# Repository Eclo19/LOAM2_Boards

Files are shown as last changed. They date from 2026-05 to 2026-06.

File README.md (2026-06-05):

# LOAM2_Boards_Winter/Spring_2026

## Description
These files contain the progress done on drone hardware for the LOAM 2 project. The current strategy is to produce a support board that connects to the Pixhawk's FMU, communicates with the nodes, and hosts many other vital systems. This board should concentrate as many of the drone peripherals as possible in a single PCB to ensure robustness. The support board contains the following sub-systems:

 * Power management and battery monitoring (PM)
 * GPS
 * ARM Switch
 * nRF54L15 (MCU)
 * nRF21540 (FEM)
 * GPS patch antenna
 * Bluetooth antenna (not certain yet)
 * JST Connectors for the FMU harness
 * Debug taps for all outputs

## Power Management

The power management issue is mostly solved. The board stored in `power_management_tests` was produced and thoroughly tested. We confirmed its outputs were the expected 3.3 and 5V, it handled the throuttle of the drone motors, and voltage and current readings are in agreement with lab equipment. **Note:** To ensure proper voltage and current readings, the resistor ratios implemented in the voltage and current sensors must be taken into account by the software. In Ardupilot, simply set `BATT_VOLT_MULT = 5.667` and `BATT_AMP_PERVLT = 25.0`. The chosen buck-converters can output currents of up to 3 A, far more than the FMU or the support board systems might draw. 

When redoing the layout for this board in the support board, make sure to follow IC datasheet recommendations and lay thick traces in the battery input and output ports, which can draw large currents (~80 A). 

## GPS

The GPS schematics were adapted from this repository: https://github.com/ZIOCC/Zio-Qwiic-GPS-Module-U-blox-NEO-M8N-0-10). They leverage the NEO-M8N-0 chip and a patch antenna at the GPS band of 1575.42 MHz. 

## Arm Switch

This replaces the floating ARM switch in the Pixhawk. 

## MCU and FEM

The drone communicates with node sensors through the nRF54L15 MCU using BLE. Currently, we assume the nodes will also host this MCU, as inter-communication between this IC is simple. The MCU is powered by the 3.3 V power line produced by the PM. Communication with the FMU is done through the TELEM2 port, which connects through UART to pins on the suppoart board MCU. 

The current drone wake-up strategy is to rely on energy harvesting to charge the base of an $npn$ transistor (2N3904) above its $V_{th}$, flipping the collector voltage from 3.3 V to 0 when charged, thus waking up the node. The node MCU must handle this and a few nuances regarding oscillation (described in our report) in firmware. We used the AEM30940 DK for our energy harvesting tests on the chosen band of 2.45 GHz. To ensure enough energy can be transmitted to charge the base of the transistor to around 0.65 V, a decent amount of power must be received. The The 47 C.F.R. § 15.247 permits a maximum of 1 W (30 dBm) of transmission power for the 2.45 GHz band given a few constraints, and the nRF54L15 can ony output a maximum of 8 dBm. To increase transmission power, we connect an RF FEM, the nRF21540, a bidirectional FEM (LNA for Rx and PA for Tx, with shiwtching controlled by GPIO pins or SPI). The antenna choice is still a major question for this transmission. 

The drone MCU in the suppoart board is programmed through an SWD interface. 

## Connectors and Debug Taps

The support board hosts multiple connectors that should be tightly packed in a harness connected to the FMU. These include the following ports: GPS, TELEM2, SWITCH, and POWER. Our initial connector selection was a DF13, but these are not fully compatible. We believe the correct connectors are JST. For testing and debugging reasons, it is helpful to pack debup taps for many essential nodes in the system (e.g. 3V3, 5V, CURRENT_SENSE, RX_GPS, etc). 

## Layout Notes

The layout of the support board has just started at the time of this README.md file. Like in the power management test board, the support board has DRCs from JLC PCB, imported from https://github.com/sethhillbrand/kicad_templates/tree/master. This board has 4 layers though, as opposed to the simple 2-layer power management tests board.

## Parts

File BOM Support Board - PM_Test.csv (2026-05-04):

Reference | Qty | Value | Manufacturer | Manufacturer Product Number | Description | Footprint | Datasheet | Notes
C501,C502 | 2 | 10 u | Murata Electronics | CAP CER 10UF 6.3V X5R 0603 | CAP CER 10UF 6.3V X5R 0603 | Capacitor_SMD:C_0603_1608Metric_Pad1.08x0.95mm_HandSolder | ~
C503,C505,C510,C512,C516,C517, | 6 | 100n | Samsung Electro-Mechanics | CL10E104KC8VPNC | CAP CER 100NF 100V X8L 0603 | Capacitor_SMD:C_0603_1608Metric_Pad1.08x0.95mm_HandSolder | ~
C504,C511 | 2 | 22 n | Samsung Electro-Mechanics | CL10B223KB8WPNC | CAP CER 0.022UF 50V X7R 0603 | Capacitor_SMD:C_0603_1608Metric_Pad1.08x0.95mm_HandSolder | ~
C506,C507,C509,C513,C514 | 5 | 22µ | Venkel | C0805X5R350-226MNE-CT | Chip Capacitor,0805,X5R,35V,22uF | Capacitor_SMD:C_0805_2012Metric_Pad1.18x1.45mm_HandSolder | ~
C508 | 1 | 470p | Samsung Electro-Mechanics | CL10C471JB8NNNC | CAP CER 470PF 50V C0G/NP0 0603 | Capacitor_SMD:C_0603_1608Metric_Pad1.08x0.95mm_HandSolder | ~
C515 | 1 | 300p | KYOCERA AVX | 06035A301JAT2A | CAP CER 300PF 50V NP0 0603 | Capacitor_SMD:C_0603_1608Metric_Pad1.08x0.95mm_HandSolder | ~
C518 | 1 | 1µ | Samsung Electro-Mechanics | CL10B105KP8NNNC | CAP CER 1UF 10V X7R 0603 | Capacitor_SMD:C_0603_1608Metric_Pad1.08x0.95mm_HandSolder | ~
D1 | 1 | RED | Rohm Semiconductor | SML-D12U1WT86 | LED RED DIFFUSED 1608 SMD | LED_SMD:LED_0603_1608Metric_Pad1.05x0.95mm_HandSolder | ~
D2 | 1 | Yellow | Rohm Semiconductor | SML-D12Y1WT86 | LED YELLOW DIFFUSED 1608 SMD | LED_SMD:LED_0603_1608Metric_Pad1.05x0.95mm_HandSolder | ~
J1,J4 | 2 | Conn_01x02_Socket |  |  |  | Connector_Wire:SolderWire-6sqmm_1x02_P14mm_D3.5mm_OD7mm | ~
J2,J3,J6,J7 | 4 | Conn_01x02_Socket |  |  |  | Connector_Wire:SolderWire-0.75sqmm_1x02_P7mm_D1.25mm_OD3.5mm | ~
J5 | 1 | Conn_01x06_Pin | Hirose Electric Co Ltd | DF13-6P-1.25DSA(05) | CONNECTOR | Connector_Hirose:Hirose_DF13-06P-1.25DSA_1x06_P1.25mm_Vertical | ~
J505 | 1 | Conn_01x01_Socket |  |  |  | Connector_Wire:SolderWire-0.75sqmm_1x01_D1.25mm_OD3.5mm | ~
L501,L502 | 2 | 6.8µH | TDK | MLZ2012N6R8LT000 | FIXED IND 6.8UH 550MA 250 MOHM | Inductor_SMD:L_0805_2012Metric_Pad1.05x1.20mm_HandSolder | ~
R501,R507 | 2 | 191k | YAGEO | RC0603FR-07191KL | RES 191K OHM 1% 1/10W 0603 | Resistor_SMD:R_0603_1608Metric_Pad0.98x0.95mm_HandSolder | ~
R502,R508 | 2 | 49.9k | YAGEO | RC0603FR-0749K9L | RES 49.9K OHM 1% 1/10W 0603 | Resistor_SMD:R_0603_1608Metric_Pad0.98x0.95mm_HandSolder | ~
R503 | 1 | 100k | YAGEO | RC0603FR-07100KL | RES 100K OHM 1% 1/10W 0603 | Resistor_SMD:R_0603_1608Metric_Pad0.98x0.95mm_HandSolder | ~
R504,R509,R510,R511 | 4 | 10k | YAGEO | RC0603FR-0710KL | RES 10K OHM 1% 1/10W 0603 | Resistor_SMD:R_0603_1608Metric_Pad0.98x0.95mm_HandSolder | ~
R505 | 1 | 9.09k | YAGEO | RC0603FR-079K09L | RES 9.09K OHM 1% 1/10W 0603 | Resistor_SMD:R_0805_2012Metric_Pad1.20x1.40mm_HandSolder | ~
R506 | 1 | 51k | YAGEO | RC0603FR-0751KL | RES 51K OHM 1% 1/10W 0603 | Resistor_SMD:R_0603_1608Metric_Pad0.98x0.95mm_HandSolder | ~
R512 | 1 | 90.9k | YAGEO | RC0603FR-0790K9L | RES 90.9K OHM 1% 1/10W 0603 | Resistor_SMD:R_0603_1608Metric_Pad0.98x0.95mm_HandSolder | ~
R513 | 1 | 56k | YAGEO | RC0603FR-0756KL | RES 56K OHM 1% 1/10W 0603 | Resistor_SMD:R_0603_1608Metric_Pad0.98x0.95mm_HandSolder | ~
R514 | 1 | 12k | YAGEO | RC0603FR-0712KL | RES 12K OHM 1% 1/10W 0603 | Resistor_SMD:R_0603_1608Metric_Pad0.98x0.95mm_HandSolder | ~
R515 | 1 | 0.5m | Vishay Dale | WSLF2512L5000FEB | RES SMD 500 UOHM 1% 6W 2512 | Resistor_SMD:R_2512_6332Metric_Pad1.40x3.35mm_HandSolder | ~
R516 | 1 | 80k | Vishay Dale Thin Film | PTN0603E8002BST1 | RES 80K OHM 0.1% 0.15W 0603 | Resistor_SMD:R_0603_1608Metric_Pad0.98x0.95mm_HandSolder
R517,R518 | 2 | 1K ±1% | YAGEO | RC0603FR-071KL | RES 1K OHM 1% 1/10W 0603 | Resistor_SMD:R_0603_1608Metric_Pad0.98x0.95mm_HandSolder
U501,U502 | 2 | ~ | Monolithic Power Systems Inc. | MP2338GTL-Z | IC REG BUCK ADJ 3A SOT583 | Package_TO_SOT_SMD:SOT-583-8
U503 | 1 | INA169 | Texas Instruments | INA169NA/3K | IC CURRENT MONITOR 0.5% SOT23-5 | Package_TO_SOT_SMD:SOT-23-5 | http://www.ti.com/lit/ds/symlink/ina169.pdf
U504 | 1 | MCP6002T-E/OT | Microchip Technology | MCP6002-I/P | IC OPAMP GP 2 CIRCUIT 8DIP | Package_DIP:DIP-8_W7.62mm_LongPads | https://ww1.microchip.com/downloads/en/DeviceDoc/MCP6001-1R-1U-2-4-1-MHz-Low-Power-Op-Amp-DS20001733L.pdf

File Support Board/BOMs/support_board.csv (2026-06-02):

Reference | Qty | Value | DNP | Exclude from BOM | Exclude from Board | Footprint | Datasheet
C101 | 1 | 22pF ±10% 50V |  |  |  | Capacitor_SMD:C_0402_1005Metric_Pad0.74x0.62mm_HandSolder
C102 | 1 | 33pF ±10% 50V |  |  |  | Capacitor_SMD:C_0402_1005Metric_Pad0.74x0.62mm_HandSolder
C103 | 1 | 4.7uF ±10% 10V |  |  |  | Capacitor_SMD:C_0402_1005Metric_Pad0.74x0.62mm_HandSolder
C104,C105,C107,C110 | 4 | 100nF ±10% 50V |  |  |  | Capacitor_SMD:C_0402_1005Metric_Pad0.74x0.62mm_HandSolder
C106 | 1 | 10uF ±10% 10V |  |  |  | Capacitor_SMD:C_0402_1005Metric_Pad0.74x0.62mm_HandSolder
C108 | 1 | XH414HG-IV01E |  |  |  | Capacitor_SMD:C_1210_3225Metric
C301,C302 | 2 | 12pF |  |  |  | Capacitor_SMD:C_0402_1005Metric_Pad0.74x0.62mm_HandSolder | ~
C303,C305,C306,C307,C308 | 5 | 100nF |  |  |  | Capacitor_SMD:C_0402_1005Metric_Pad0.74x0.62mm_HandSolder | ~
C304 | 1 | 22 uF |  |  |  | Capacitor_SMD:C_0603_1608Metric_Pad1.08x0.95mm_HandSolder | ~
C309 | 1 | 0.3pF |  |  |  | Capacitor_SMD:C_0603_1608Metric_Pad1.08x0.95mm_HandSolder | ~
C310 | 1 | 0.5pF |  |  |  | Capacitor_SMD:C_0402_1005Metric_Pad0.74x0.62mm_HandSolder | ~
C311 | 1 | 10nF |  |  |  | Capacitor_SMD:C_0402_1005Metric_Pad0.74x0.62mm_HandSolder | ~
C501,C502 | 2 | 10 u |  |  |  | Capacitor_SMD:C_01005_0402Metric_Pad0.57x0.30mm_HandSolder | ~
C503,C510,C516,C517 | 4 | 100n |  |  |  | Capacitor_SMD:C_01005_0402Metric_Pad0.57x0.30mm_HandSolder | ~
C504,C511 | 2 | 22 n |  |  |  | Capacitor_SMD:C_01005_0402Metric_Pad0.57x0.30mm_HandSolder | ~
C505,C512 | 2 | 100 n |  |  |  | Capacitor_SMD:C_01005_0402Metric_Pad0.57x0.30mm_HandSolder | ~
C506,C513 | 2 | 22u |  |  |  | Capacitor_SMD:C_01005_0402Metric_Pad0.57x0.30mm_HandSolder | ~
C507,C514 | 2 | 22µ |  |  |  | Capacitor_SMD:C_01005_0402Metric_Pad0.57x0.30mm_HandSolder | ~
C508 | 1 | 470p |  |  |  | Capacitor_SMD:C_01005_0402Metric_Pad0.57x0.30mm_HandSolder | ~
C509 | 1 | 22 u |  |  |  | Capacitor_SMD:C_01005_0402Metric_Pad0.57x0.30mm_HandSolder | ~
C515 | 1 | 300p |  |  |  | Capacitor_SMD:C_01005_0402Metric_Pad0.57x0.30mm_HandSolder | ~
C518 | 1 | 1µ |  |  |  | Capacitor_SMD:C_01005_0402Metric_Pad0.57x0.30mm_HandSolder | ~
D101 | 1 | RB520S30T1G |  |  |  | Diode_SMD:D_SOD-523
D103 | 1 | GREEN |  |  |  | LED_SMD:LED_0603_1608Metric
D201,D501 | 2 | RED |  |  |  | LED_SMD:LED_0603_1608Metric | ~
D502 | 1 | YELLOW |  |  |  | LED_SMD:LED_0603_1608Metric
E101 | 1 | APAE1575R1820ABDC1-T |  |  |  | support_board:XDCR_APAE1575R1820ABDC1-T
GPS_CONN1,POWER_CONN1,TELEM2_CONN1 | 3 | Conn_01x06_Socket |  |  |  | Connector_Hirose:Hirose_DF13-06P-1.25DSA_1x06_P1.25mm_Vertical | ~
GPS_DEBUG1 | 1 | Conn_01x04_Socket |  |  |  | Connector_Wire:SolderWire-0.75sqmm_1x04_P4.8mm_D1.25mm_OD2.3mm | ~
J301 | 1 | Conn_Coaxial |  |  |  | Connector_Coaxial:U.FL_Hirose_U.FL-R-SMT-1_Vertical | ~
J302 | 1 | Conn_ARM_SWD_TagConnect_TC2030-NL |  | Excluded from BOM |  | Connector:Tag-Connect_TC2030-IDC-NL_2x03_P1.27mm_Vertical | https://www.tag-connect.com/wp-content/uploads/bsk-pdf-manager/TC2030-CTX_1.pdf
J503,J504,J505 | 3 | Conn_01x01_Socket |  |  |  | Connector_Wire:SolderWire-0.75sqmm_1x01_D1.25mm_OD3.5mm | ~
L101 | 1 | 22uH ±10% |  |  |  | Inductor_SMD:L_0603_1608Metric
L301 | 1 | 2nH |  |  |  | Inductor_SMD:L_0402_1005Metric_Pad0.77x0.64mm_HandSolder | ~
L501,L502 | 2 | 6.8µH |  |  |  | Inductor_SMD:L_0402_1005Metric | ~
R101,R107,R109 | 3 | 1K ±1% |  |  |  | Resistor_SMD:R_0402_1005Metric_Pad0.72x0.64mm_HandSolder
R102,R103 | 2 | 10K ±1% |  |  |  | Resistor_SMD:R_0402_1005Metric_Pad0.72x0.64mm_HandSolder
R104,R105 | 2 | 4.7K ±1% |  |  |  | Resistor_SMD:R_0402_1005Metric_Pad0.72x0.64mm_HandSolder
R108 | 1 | 22R ±1% |  |  |  | Resistor_SMD:R_0402_1005Metric_Pad0.72x0.64mm_HandSolder
R201 | 1 | 220 |  |  |  | Resistor_SMD:R_0402_1005Metric_Pad0.72x0.64mm_HandSolder | ~
R301 | 1 | 10k |  |  |  | Resistor_SMD:R_0402_1005Metric_Pad0.72x0.64mm_HandSolder | ~
R302,R303 | 2 | 100 |  |  |  | Resistor_SMD:R_0402_1005Metric_Pad0.72x0.64mm_HandSolder | ~
R501,R507 | 2 | 191k |  |  |  | Resistor_SMD:R_0603_1608Metric_Pad0.98x0.95mm_HandSolder | ~
R502,R508 | 2 | 49.9k |  |  |  | Resistor_SMD:R_0603_1608Metric_Pad0.98x0.95mm_HandSolder | ~
R503 | 1 | 100k |  |  |  | Resistor_SMD:R_0603_1608Metric_Pad0.98x0.95mm_HandSolder | ~
R504,R509,R510,R511,R516 | 5 | 10k |  |  |  | Resistor_SMD:R_0603_1608Metric_Pad0.98x0.95mm_HandSolder | ~
R505 | 1 | 9.09k |  |  |  | Resistor_SMD:R_0603_1608Metric_Pad0.98x0.95mm_HandSolder | ~
R506 | 1 | 51k |  |  |  | Resistor_SMD:R_0603_1608Metric_Pad0.98x0.95mm_HandSolder | ~
R512 | 1 | 90.9k |  |  |  | Resistor_SMD:R_0603_1608Metric_Pad0.98x0.95mm_HandSolder | ~
R513 | 1 | 56k |  |  |  | Resistor_SMD:R_0603_1608Metric_Pad0.98x0.95mm_HandSolder | ~
R514 | 1 | 12k |  |  |  | Capacitor_SMD:C_0805_2012Metric_Pad1.18x1.45mm_HandSolder | ~
R515 | 1 | 4m |  |  |  | Resistor_SMD:R_0603_1608Metric_Pad0.98x0.95mm_HandSolder | ~
R517,R518 | 2 | 1K ±1% |  |  |  | Resistor_SMD:R_0603_1608Metric_Pad0.98x0.95mm_HandSolder
SWITCH1 | 1 | 1825910-6 |  |  |  | support_board:SW_1825910-6-4
SWITCH_CONN1 | 1 | Conn_01x03_Socket |  |  |  | Connector_Hirose:Hirose_DF13-03P-1.25DSA_1x03_P1.25mm_Vertical | ~
SWITCH_DEBUG1 | 1 | Conn_01x03_Socket |  |  |  | Connector_Wire:SolderWire-0.75sqmm_1x03_P4.8mm_D1.25mm_OD2.3mm | ~
TELEM_2_DEBUG1 | 1 | Conn_01x02_Socket |  |  |  | Connector_Wire:SolderWire-0.75sqmm_1x02_P4.8mm_D1.25mm_OD2.3mm | ~
U101 | 1 | NEO-M8N |  |  |  | support_board:NEO-M8N-0
U102 | 1 | SC16IS752 |  |  |  | support_board:SC16IS752
U301 | 1 | nRF54L15-QFXX |  |  |  | Package_DFN_QFN:QFN-48-1EP_6x6mm_P0.4mm_EP4.6x4.6mm | https://docs.nordicsemi.com/bundle/ps_nrf54L15
U501,U502 | 2 | MP2338 |  |  |  | Package_TO_SOT_SMD:SOT-583-8
U503 | 1 | INA169 |  |  |  | Package_TO_SOT_SMD:SOT-23-5 | http://www.ti.com/lit/ds/symlink/ina169.pdf
U504 | 1 | MCP6002T-E/OT |  |  |  | Package_DIP:DIP-8_W7.62mm_LongPads | https://ww1.microchip.com/downloads/en/DeviceDoc/MCP6001-1R-1U-2-4-1-MHz-Low-Power-Op-Amp-DS20001733L.pdf
X101 | 1 | 3.072MHZ |  |  |  | Crystal:Crystal_SMD_HC49-SD
X201 | 1 | Crystal_GND24 |  |  |  | Crystal:Crystal_SMD_2016-4Pin_2.0x1.6mm | ~

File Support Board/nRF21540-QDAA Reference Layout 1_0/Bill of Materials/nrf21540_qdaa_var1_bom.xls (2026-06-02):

Bill of material
Board: | nRF21540 Reference Layout Alt. 1
Version: | 1.0
Designator | Value | Description | Footprint Doc
C1, C3 | 1.0pF | Capacitor, NP0, ±0.05pF, 50V | 0201
C2 | 2.0pF | Capacitor, NP0, ±0.05pF, 25V | 0201
C6 | 100nF | Capacitor, X5R, ±10% | 0201
C7 | 10µF | Capacitor, X5R, ±20% | 0603
L1 | 1.9nH | Inductor, 600mA, ±0.1ｎH, 120mOhm | 0201
L2 | 3.0nH | Inductor, 600mA, ±0.1ｎH, 120mOhm | 0201
R1 | 33k | Resistor, ±1%, 0.05W | 0201
R2 | 49.9R | Resistor, ±1%, 0.05W | 0201
U1 | nRF21540-QDAA | Radio front-end / range extender for 2.4GHz | QFN-16

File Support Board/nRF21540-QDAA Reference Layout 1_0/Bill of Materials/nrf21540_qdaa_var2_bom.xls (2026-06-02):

Bill of material
Board: | nRF21540 Reference Layout Alt. 2
Version: | 1.0
Designator | Value | Description | Footprint Doc
C1, C3, C5 | 1.0pF | Capacitor, NP0, ±0.05pF, 50V | 0201
C2, C4 | 2.0pF | Capacitor, NP0, ±0.05pF, 25V | 0201
C6 | 100nF | Capacitor, X5R, ±10% | 0201
C7 | 10µF | Capacitor, X5R, ±20% | 0603
L1, L3 | 1.9nH | Inductor, 600mA, ±0.1ｎH, 120mOhm | 0201
L2, L4 | 3.0nH | Inductor, 600mA, ±0.1ｎH, 120mOhm | 0201
R1 | 33k | Resistor, ±1%, 0.05W | 0201
U1 | nRF21540-QDAA | Radio front-end / range extender for 2.4GHz | QFN-16

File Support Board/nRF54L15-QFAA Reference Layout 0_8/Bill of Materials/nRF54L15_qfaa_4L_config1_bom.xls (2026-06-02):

Bill of material
Device: | nRF54L15-QFAA
Title: | Reference Layout
Version: | v0.8
Designator | Value | Description | Assembly | Footprint Doc
C1, C2 | 2.2µF | Capacitor, Ceramic, 2.2µF 2.5V X6T 0201,±20% |  | 0201
C3 | 10µF | Capacitor, X6S, ±20%, 6.3V |  | 0402
C4, C7, C8, C10 | 100nF | Capacitor, X7R, ±10% |  | 0201
C5 | 2.2nF | Capacitor, X7R, ±10%, 10V |  | 0201
C6 | 1.5pF | Capacitor, NP0, ±0.05pF, 25V |  | 0201
C9 | 2.0pF | Capacitor, NP0, ±0.05pF, 25V |  | 0201
C11 | 0.3pF | Capacitor, C0G, ±0.1pF, 50V |  | 0201
C12 | 10nF | Capacitor, X7R, 6.3V |  | 0201
C13 | 3.9pF | Capacitor, NP0, ±0.05pF, 25V |  | 0201
FB1 | 120R/0.2A | Ferrite Bead, 120 Ohm @ 100MHz, 200mA, 500 mOhm Max |  | 0201
L1 | 4.7µH | Inductor, 120mA, ±20%, 0.65R |  | 0603
L2 | 2.7nH | Inductor, 600mA, ±0.1ｎH, 120mOhm |  | 0201
L3, L4 | 3.5nH | Inductor, 500mA, ±0.1ｎH, 170mOhm |  | 0201
R1 | 1k | Resistor, ±1%, 0.05W |  | 0201
U1 | nRF54L15-QFAA | Multi-protocol Bluetooth Low Energy, IEEE 802.15.4 and 2.4GHz proprietary Wireless MCU |  | QFN-48
X1 | 32.768kHz | XTAL SMD 2012, 32.768kHz, 9pF, ±20ppm |  | XTAL_2012
X2 | 32MHz | XTAL SMD 2016, 32MHz, Cl=8pF, Tot: ±40ppm |  | XTAL_2016

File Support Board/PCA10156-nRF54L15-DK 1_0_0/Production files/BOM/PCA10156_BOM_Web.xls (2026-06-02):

Bill of material
Board: | PCA10156
Version: | 1.0.0
Designator | Value | Description | Assembly | Footprint Doc | Manufacturer | Manufacturer Part Number
C1, C2 | 2.2µF | Capacitor, Ceramic, 2.2µF 2.5V X6T 0201,±20% |  | 0201 | Murata | GRM033R61A225KE47
C3 | 10µF | Capacitor, X6S, ±20%, 6.3V |  | 0402 | N.A. | N.A.
C4, C7, C8, C10, C11, C13, C14, C15, C18, C20, C21, C22, C25, C29, C34, C35, C36, C37, C44, C46, C48, C49, C52, C53, C55, C56, C57, C62, C63, C64, C65, C66, C69, C70, C72, C73, C74, C75, C76, C77, C78, C79 | 100nF | Capacitor, X5R, ±10% |  | 0201 | N.A. | N.A.
C5, C33 | 2.2nF | Capacitor, X7R, ±10%, 10V |  | 0201 | N.A. | N.A.
C6 | 1.5pF | Capacitor, NP0, ±0.05pF, 25V, High Q |  | 0201 | Murata | GJM0335C1E1R5WB01
C9 | 2.0pF | Capacitor, NP0, ±0.05pF, 25V |  | 0201 | Murata | GJM0335C1E2R0WB01
C12, C30 | 10nF | Capacitor, X7R, ±10% |  | 0201 | N.A. | N.A.
C16, C28, C31, C32, C39, C45, C50, C51, C68 | 1.0µF | Capacitor, X5R, ±10%, 6.3V |  | 0402 | N.A. | N.A.
C17, C19 | 300pF | Capacitor, C0G, ±5%, 50V |  | 0402 | N.A. | N.A.
C23 | 2.2µF | Capacitor, X5R, ±10% |  | 0402 | N.A. | N.A.
C24, C26, C27 | 10µF | Capacitor, X7T, ±20%, 10V |  | 0603 | Murata | GRM188D71A106MA73
C38 | 1.4pF | Capacitor, C0G, ±0.05pF, 25V |  | 0201 | Murata | GJM0335C1E1R4WB01D
C40 | 2.2µF | Capacitor, X7R, ±10%, 6.3V |  | 0603 | N.A. | N.A.
C41 | 100nF | Capacitor, X7R, ±10% |  | 0402 | N.A. | N.A.
C42, C43, C54, C58 | 4.7µF | Capacitor, X7S, ±10%, 10V |  | 0603 | N.A. | N.A.
C47 | 1.0µF | Capacitor, Ceramic, X5R, ±10%, 16V |  | 0402 | Murata | GRT155R61C105KE01D
C59 | 10nF | Capacitor, X7R, ±10%, 100V |  | 0603 | Murata | GCM188R72A103KA37D
C60 | 3.9pF | Capacitor, NP0, ±0.05pF, 25V |  | 0201 | Murata | GJM0333C1E3R9WB01
C61 | 0.3pF | Capacitor, C0G, ±0.1pF, 50V |  | 0201 | Murata | GRM0335C1HR30BA01
C67 | 10nF | Capacitor, X7R, ±10% | Not Mounted | 0201 | N.A. | N.A.
FB1 | 120R/0.2A | Ferrite Bead, 120 Ohm @ 100MHz, 200mA, 500 mOhm Max |  | 0201 | Murata | BLM03AG121SN1D
FB2, FB3 | 120R/0.55A | Ferrite Bead, 120 Ohm @ 100MHz, 500mA, 250 mOhm Max |  | 0402 | Murata | BLM15AG121SN1D
Fid1, Fid2, Fid3 | N.A. | Fiducial Mark |  | Fiducial | N.A. | N.A.
J1 | MM8130-2600 | Coaxial Connector with Switch |  | COAXIAL-SWF | Murata | MM8130-2600
J3 | USB-C 2.0 | USB-C Receptacle, 16 Pin, USB 2.0 |  | SD-80259-001 | Bellweather Electronic Corp. | SD-80259-1021
J7 | FPC 0.5mm RA SMD | 0.5mm FPC, 5P,Right Angle SMT,Double Contact,H=1.2mm,White, Tin plated |  | FPC_05P-0.5mm-RA-SMD | WCON | 5141-05RZDNWR03
JP1 | Shunt 2.54mm | Shunt Jumper 2.54mm Black, open top | Place on P6 pin 2 and 3 | SHUNT JUMPER 2.54mm | WCON | 3710-6001OS0B05
L1 | 4.7µH | Inductor, 120mA, ±20%, 0.65R |  | 0603 | TDK Corporation | MLZ1608M4R7WT000
L2 | 2.7nH | Inductor, 600mA, ±0.1ｎH, 120mOhm |  | 0201 | Murata | LQP03HQ2N7B02
L3, L4 | 3.5nH | Inductor, 500mA, ±0.1ｎH, 170mOhm |  | 0201 | Murata | LQP03HQ3N5B02
L8 | 2.2µH | Inductor, Irms=2.5A, Isat=2.9A, ±20%, DCR=73mΩ |  | 0806 | Samsung Electro-Mechanics America | CIGT201610EH2R2MNE
LABEL1 | 12x12mm | PCA version label, stick-on, 12x12mm |  | Label | Ellco Etikett | A33512‐01
LD1, LD2, LD3, LD4, LD5 | L0603G | LED, Green, 0603, 573nm, Vf=2.0V, 24mcd, - 40 to +85°C |  | 0603 | Victory Electronics | VS 25C7M5
P0, P1, P2 | Pin Hdr 2x10 | Pin Header 2x10, 2.54mm (100mil) SMD |  | HDR_2x10-SMD-2.54MM | WCON | 1125-1210S0M116CR09
P3 | Pin List 1x2 | Pin List 1x2, 2.54mm (100mil) |  | LIST_1x2 | N.A. | N.A.
P4 | Pin List 1x3 | Pin List 1x3, 2.54mm (100mil) |  | LIST_1x3 | N.A. | N.A.
P5, P6 | Pin List 1x3 | Pin List 1x3, 2.54mm (100mil), SMD |  | LIST_1x3_SMD | WCON | 1125-1103S0M116CR04
P15, P19 | Pin Header 2x5, 1.27mm | Pin Header 2x5, 1.27mm (50mil), SMD, Keying Shroud |  | HDR_2x5-SMD-1.27mm | WCON | 3132-10MS0BK00R5
P16 | Pin Header 2x10, 1.27mm | Pin Header 2x10, 1.27mm (50mil), SMD, Keying Shroud |  | HDR_2x10-SMD-1.27mm | WCON | 3132-20MS0BK00R1
P30, P31, P32 | Pin Header 2x2 SMD | Pin Header 2x2, SMD, 2.54mm (100mil) |  | HDR_2x2-SMD | WCON | 1125-1202S0M116CR03
Q1, Q2, Q3 | NX138AKS | MOSFET 2N-CH 60V 0.17A TSSOP6 (SOT363) |  | TSSOP6 | Nexperia | NX138AKSX
Q4 | PBSS4330PA | 30V, 3A, 2.1W, G=270, NPN Transistor |  | HUSON-3 (2x2) | Nexperia | PBSS4330PA,115
R1, R2, R19, R20 | 680R | Resistor, ±1%, 0.05W |  | 0201 | N.A. | N.A.
R3, R9, R38 | 0R | Resistor, ±5%, 0.05W |  | 0201 | N.A. | N.A.
R4, R37, R41, R42 | 10k | Resistor, ±1%, 0.05W |  | 0201 | N.A. | N.A.
R5 | 560R | Resistor, ±1%, 0.05W |  | 0201 | N.A. | N.A.
R6, R8, R13, R14, R15, R16, R17, R23, R31, R32, R35, R39, R56 | 100k | Resistor, ±1%, 0.05W |  | 0201 | N.A. | N.A.
R7 | 47R | Resistor, ±1%, 0.05W |  | 0201 | N.A. | N.A.
R10, R11, R12, R18, R27 | 1M0 | Resistor, ±1%, 0.05W |  | 0201 | N.A. | N.A.
R21, R22, R25, R28, R29, R30, R33, R34 | 0R | Resistor, ±5%, 0.063W |  | 0402 | N.A. | N.A.
R24 | TBD | Chip Res 0402 |  | 0402 | N.A. | N.A.
R26 | 47k | Resistor, ±1%, 0.05W |  | 0201 | N.A. | N.A.
R36 | 1k | Resistor, ±1%, 0.05W |  | 0201 | N.A. | N.A.
R40 | 2R2 | Resistor, ±1%, 0.05W |  | 0201 | N.A. | N.A.
R43 | 33k | Resistor, ±1%, 0.05W |  | 0201 | N.A. | N.A.
SW1, SW2, SW3, SW5, SW6 | PB SW | Tactile Switch, SPNO, SMD, 160gf, 6.2x6.3x2.5mm |  | Switch-PB-6.2x6.3mm-SMD | Dailywell | TS604VM1-025BR-R
SW4 | Switch | SMD slide Switch (ON-ON) |  | Switch-Slide-RA-J-Lead-DPDT-8.5x3.5mm | C&K | JS202011JAQN
TP22 | TP | PC TEST POINT TIN SMD L |  | Harwin S1751-46R | Harwin | S1751-46R
U1 | nRF54L15-QFAA | Multi-protocol Bluetooth Low Energy, IEEE 802.15.4 and 2.4GHz proprietary Wireless MCU |  | QFN-48 | Nordic Semiconductor | nRF54L15-QFAAC00
U2 | nRF5340-QKAA | Multi-protocol Bluetooth Low Energy, IEEE 802.15.4, ANT and 2.4GHz proprietary system-on-chip |  | AQFN-98 | Nordic Semiconductor | nRF5340-QKAAD0
U3, U8 | TMUX1574 | Low-Capacitance, 2:1 (SPDT) 4-Channel, analog switch |  | UFQFN-16 | Texas Instruments | TMUX1574RSVR
U4, U5, U6 | TMUX1511 | Low-Capacitance, 1:1 (SPST) 4-Channel, analog switch |  | UFQFN-16 | Texas Instruments | TMUX1511RSVR
U7, U12, U13, U14 | TXB0104 | 4-Bit Bidirectional Level-Shifter/Voltage Translator with Automatic Direction Sensing |  | 12-UFQFN | Texas Instruments | TXB0104RUTR
U9 | MX25R6435F | Ultra low power, 64M-bit, serial multi I/O flash memory |  | WSON-8 | Macronix | MX25R6435FZNIL0
U10 | nPM1300-QEAAC0 | Li-Ion/Li-Polymer USB-C battery charger with high efficiency buck regulators, LDOs or load switches, LED drivers, TWI and VBUSOUT |  | QFN-32 | Nordic Semiconductor | nPM1300-QEAAC0
U11 | ECMF02-4CMX8 | 2 Line Common mode filter with ESD protection for USB 2.0 interface |  | UFDFN-8 | STMicroelectronics | ECMF02-4CMX8
U15 | TLV271 | Dual rail to rail CMOS Amplifier |  | SOT-25 | Diodes Incorporated | TLV271CW5-7
X1 | 32.768kHz | XTAL SMD 2012, 32.768kHz, 9pF, ±20ppm |  | XTAL_2012 | TXC Corporation | 9HT11-32.768KDZC-T
X2, X3 | 32MHz | XTAL SMD 2016, 32MHz, Cl=8pF, Tol: ±10ppm, Stab: ±15ppm |  | XTAL_2016 | Golledge | MP06003

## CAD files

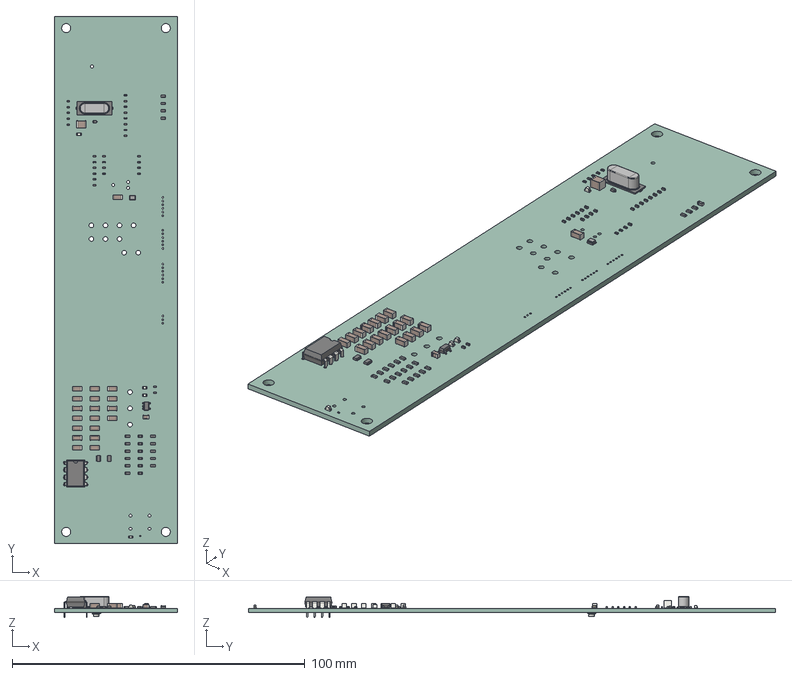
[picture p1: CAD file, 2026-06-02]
Support Board/BOMs/support_board.step
42.0 x 180.0 x 7.30 mm
C_0402_1005Metric x 18
L_0402_1005Metric x 3
C_1206_3216Metric x 19
SOT-583-8 x 2
R_0201_0603Metric
R_0603_1608Metric x 20
R_0402_1005Metric x 8
LED_0603_1608Metric x 4
D_SOD-523
L_0603_1608Metric
C_1210_3225Metric
DIP-8_W7.62mm
SOT-23-5
Crystal_SMD_2016-4Pin_2.0x1.6mm
Crystal_SMD_HC49-SD
C_0805_2012Metric
U.FL_Hirose_U.FL-R-SMT-1_Vertical
support_board_PCB

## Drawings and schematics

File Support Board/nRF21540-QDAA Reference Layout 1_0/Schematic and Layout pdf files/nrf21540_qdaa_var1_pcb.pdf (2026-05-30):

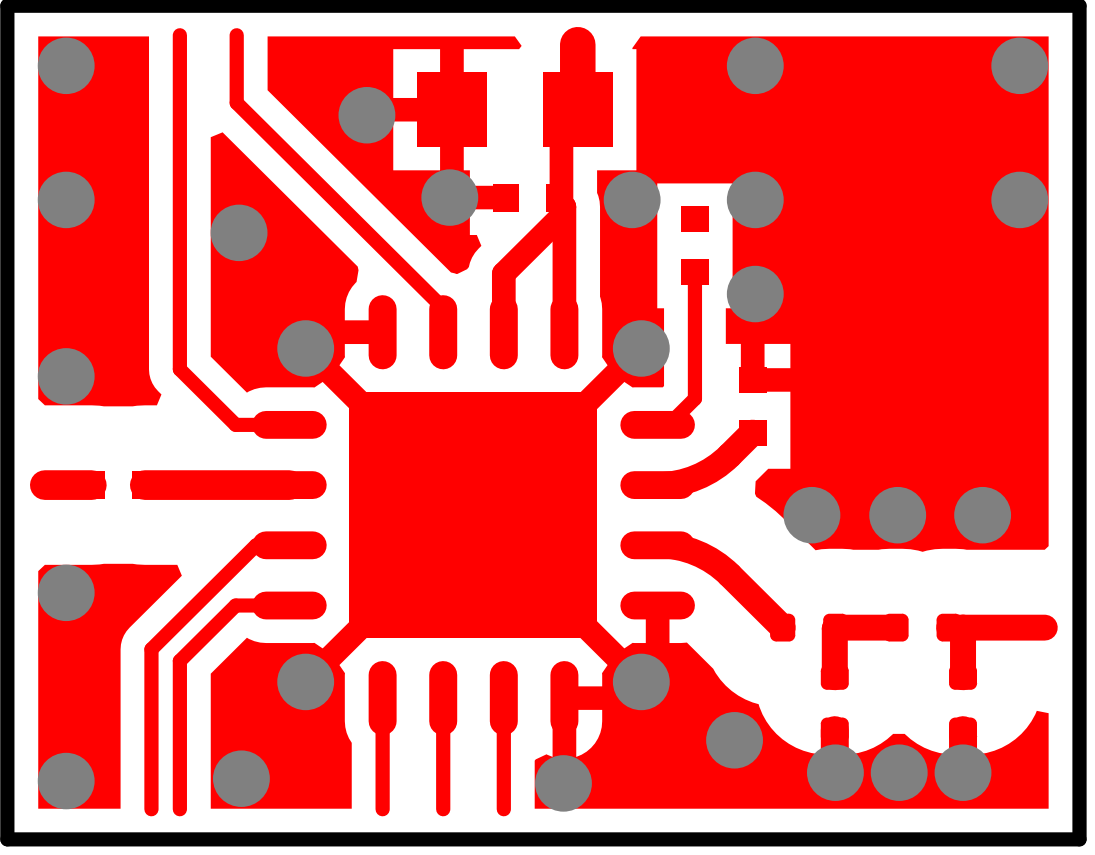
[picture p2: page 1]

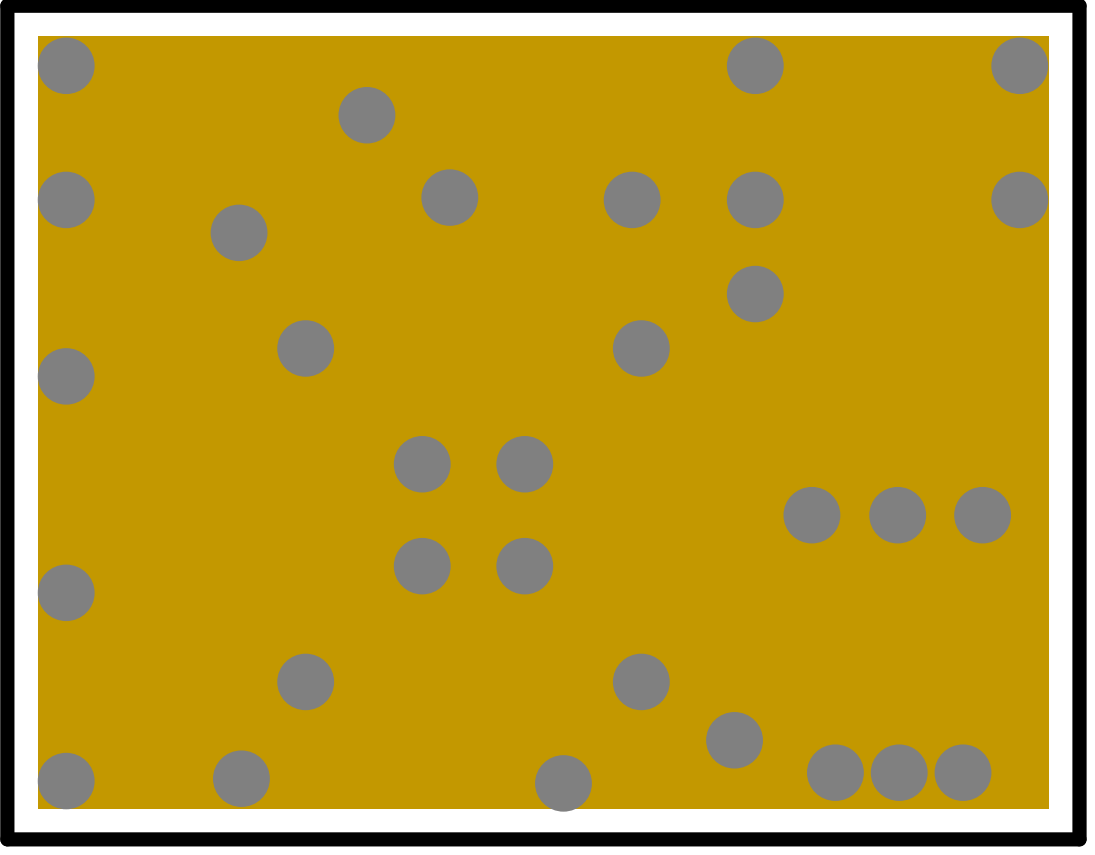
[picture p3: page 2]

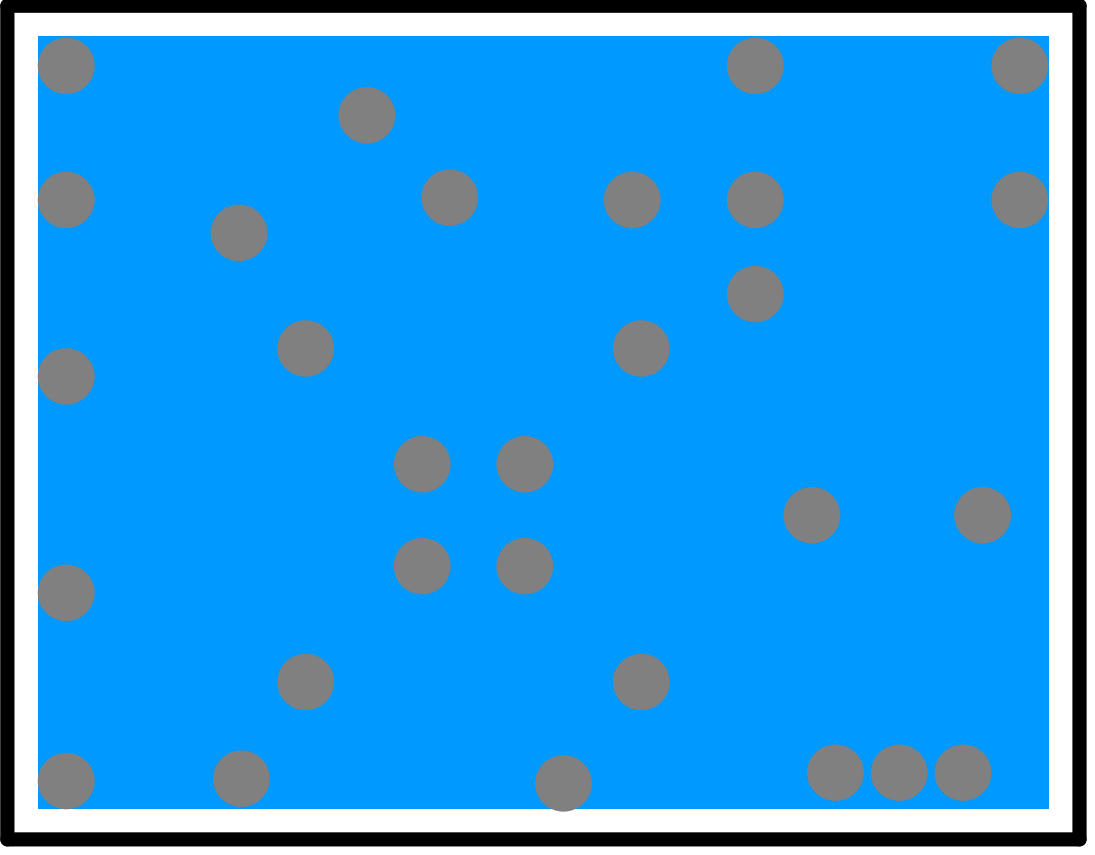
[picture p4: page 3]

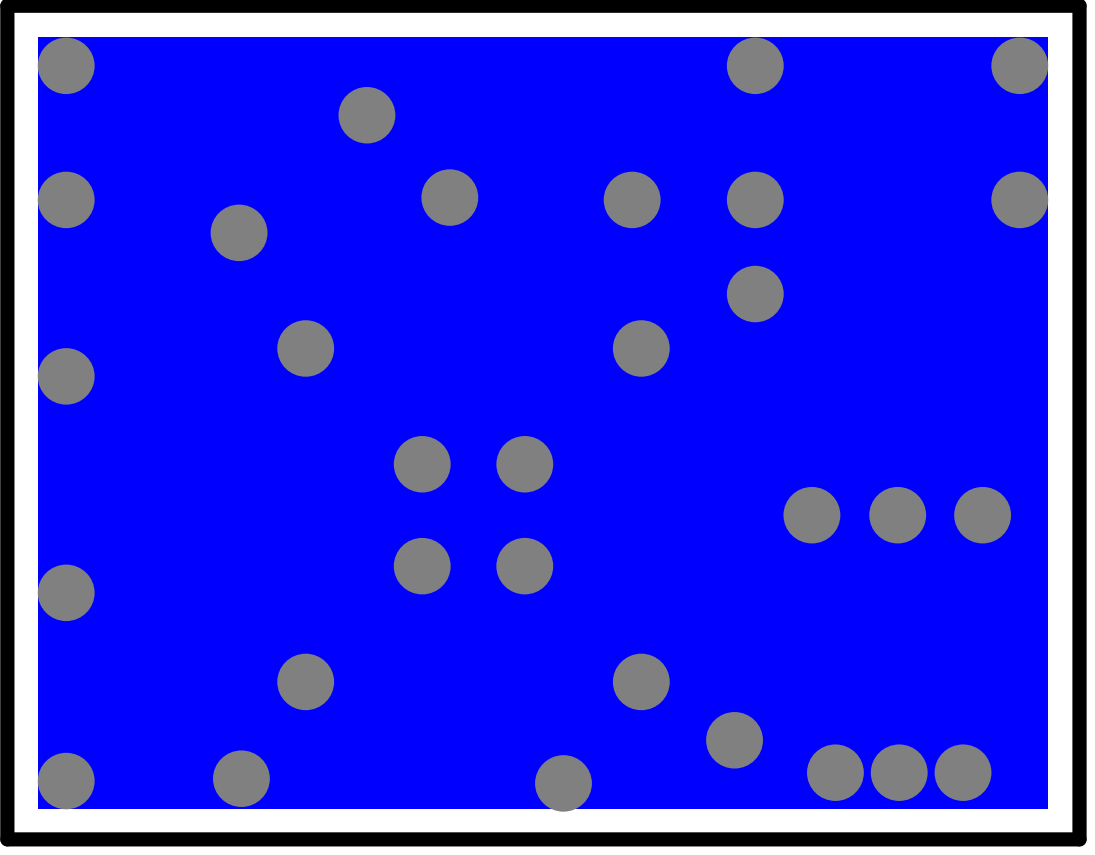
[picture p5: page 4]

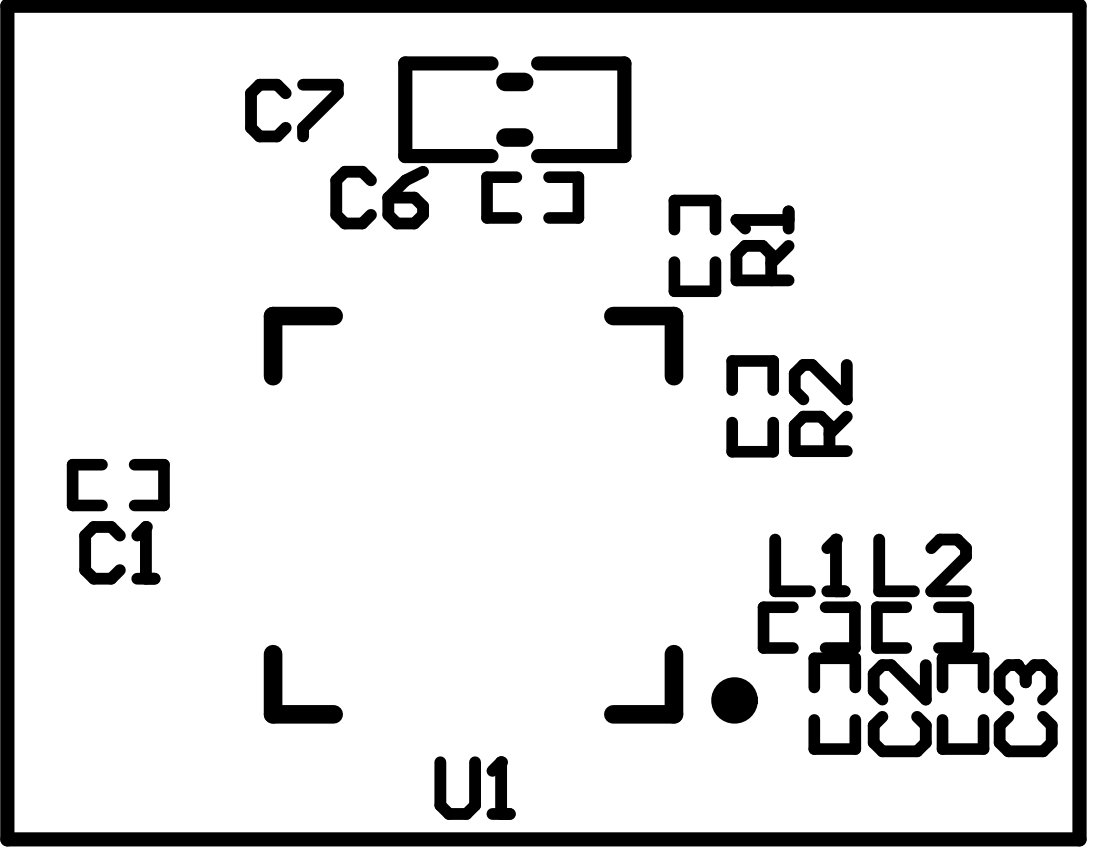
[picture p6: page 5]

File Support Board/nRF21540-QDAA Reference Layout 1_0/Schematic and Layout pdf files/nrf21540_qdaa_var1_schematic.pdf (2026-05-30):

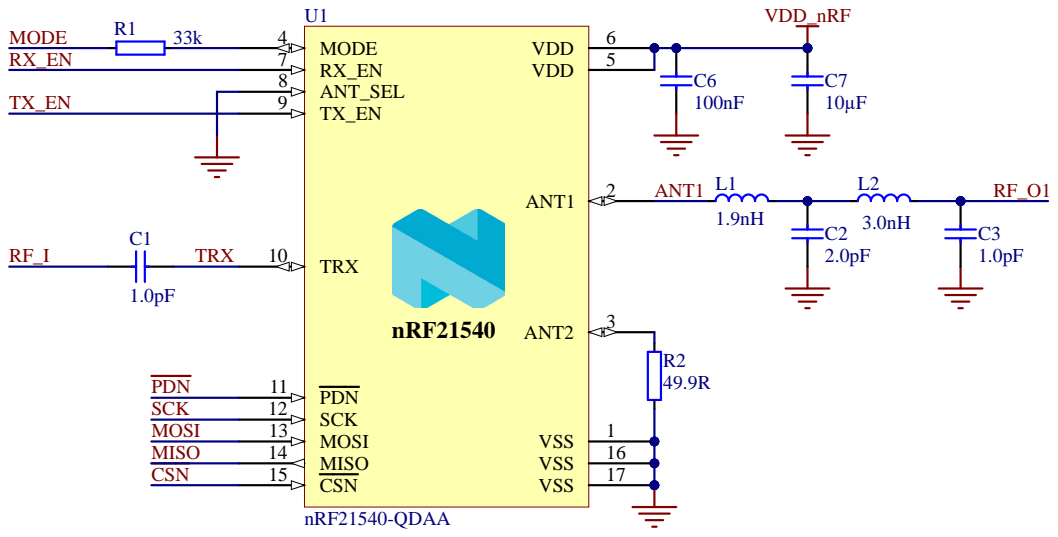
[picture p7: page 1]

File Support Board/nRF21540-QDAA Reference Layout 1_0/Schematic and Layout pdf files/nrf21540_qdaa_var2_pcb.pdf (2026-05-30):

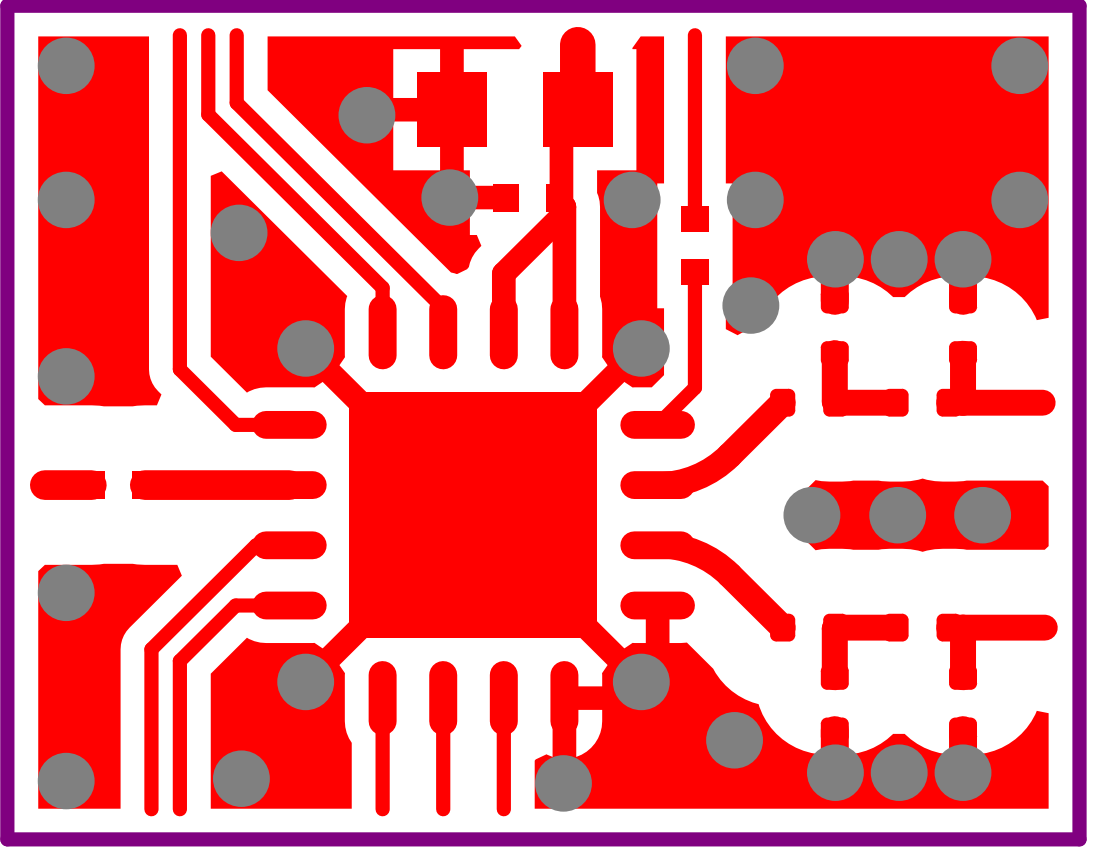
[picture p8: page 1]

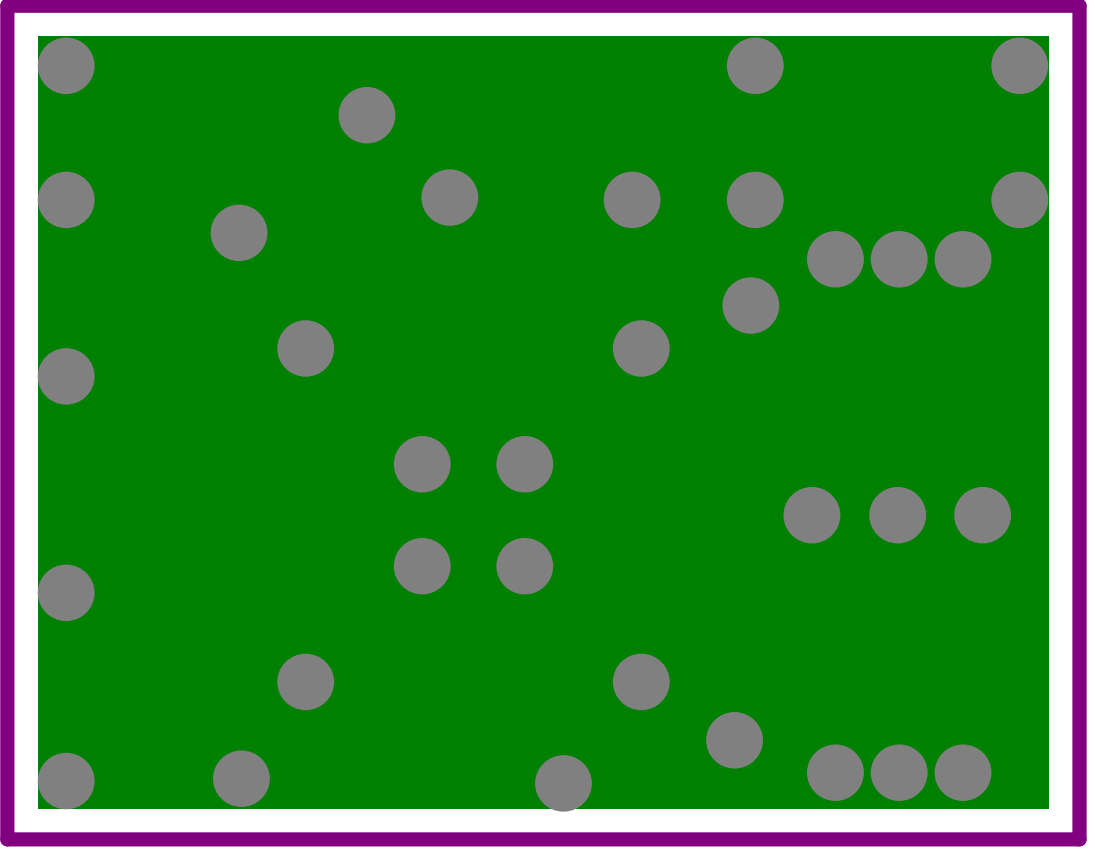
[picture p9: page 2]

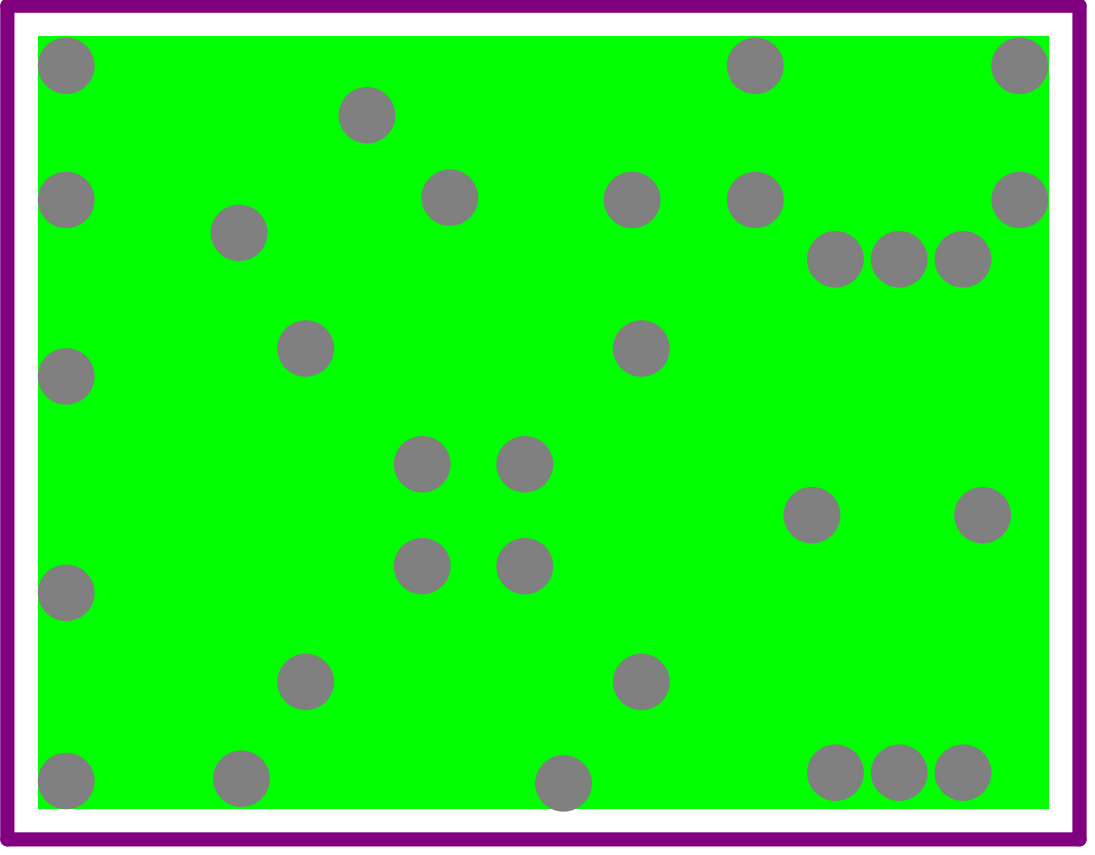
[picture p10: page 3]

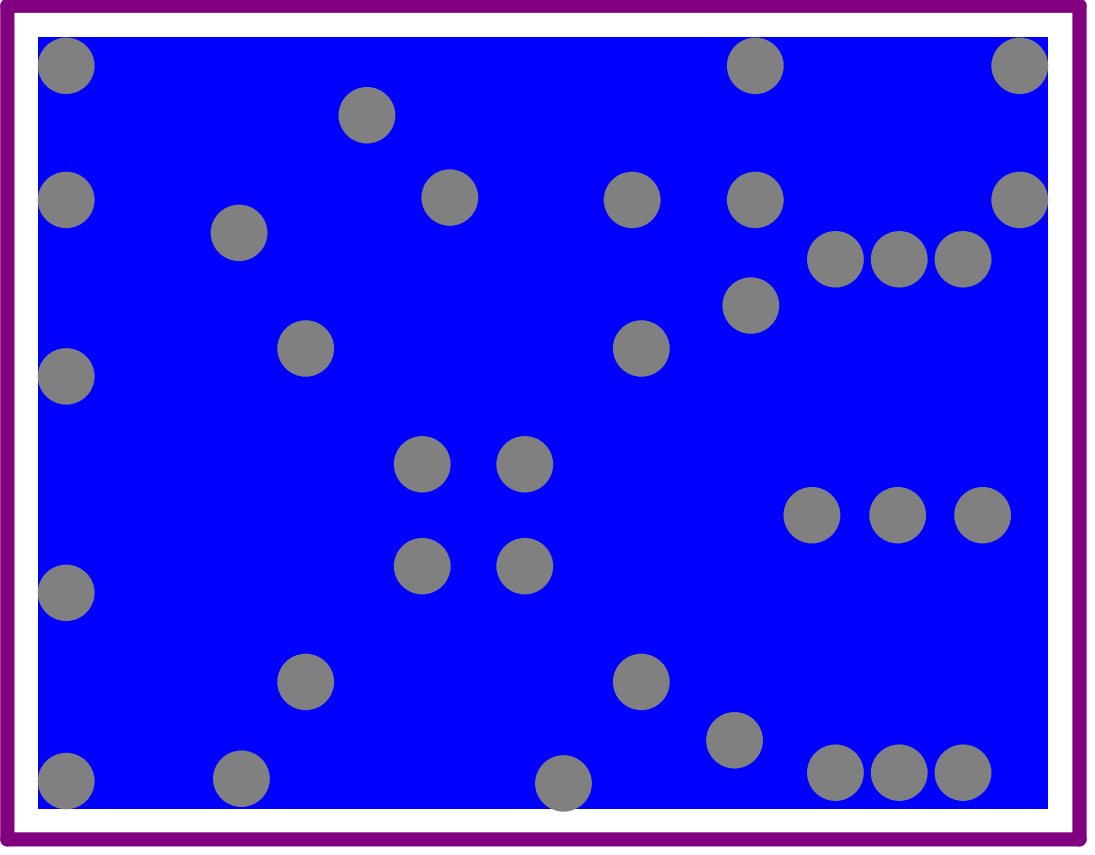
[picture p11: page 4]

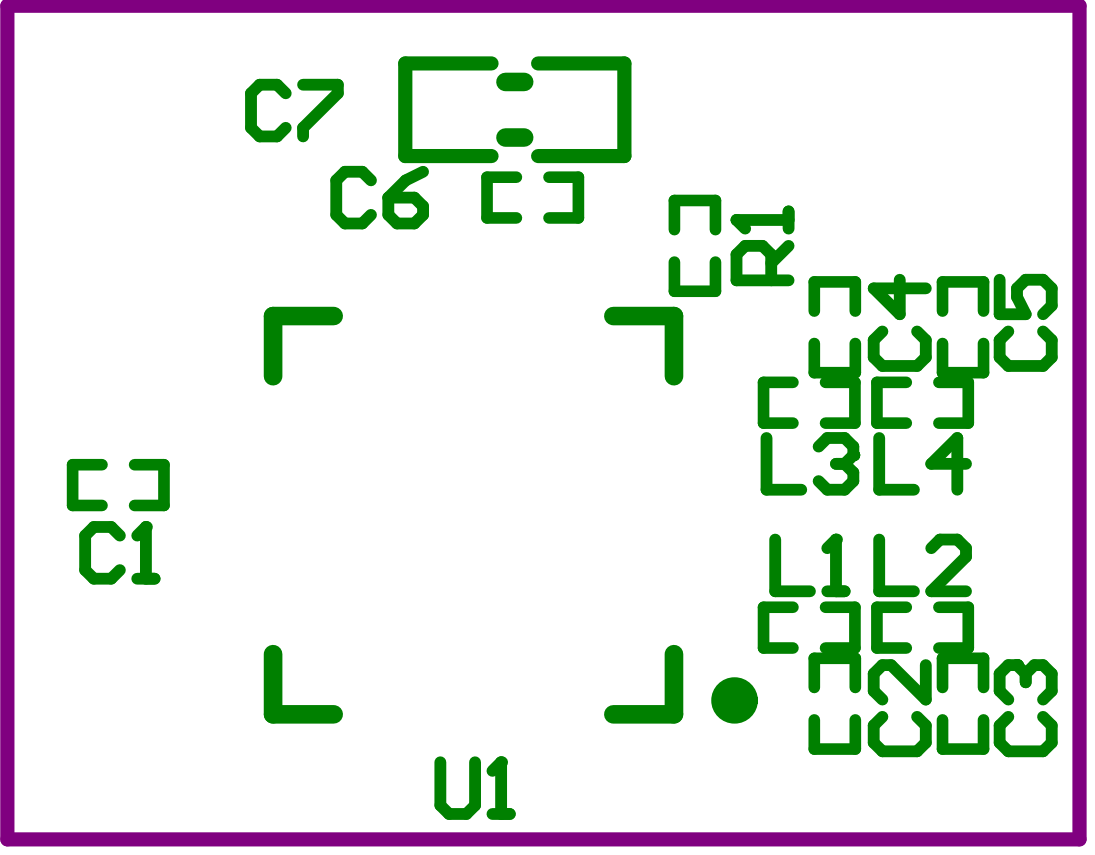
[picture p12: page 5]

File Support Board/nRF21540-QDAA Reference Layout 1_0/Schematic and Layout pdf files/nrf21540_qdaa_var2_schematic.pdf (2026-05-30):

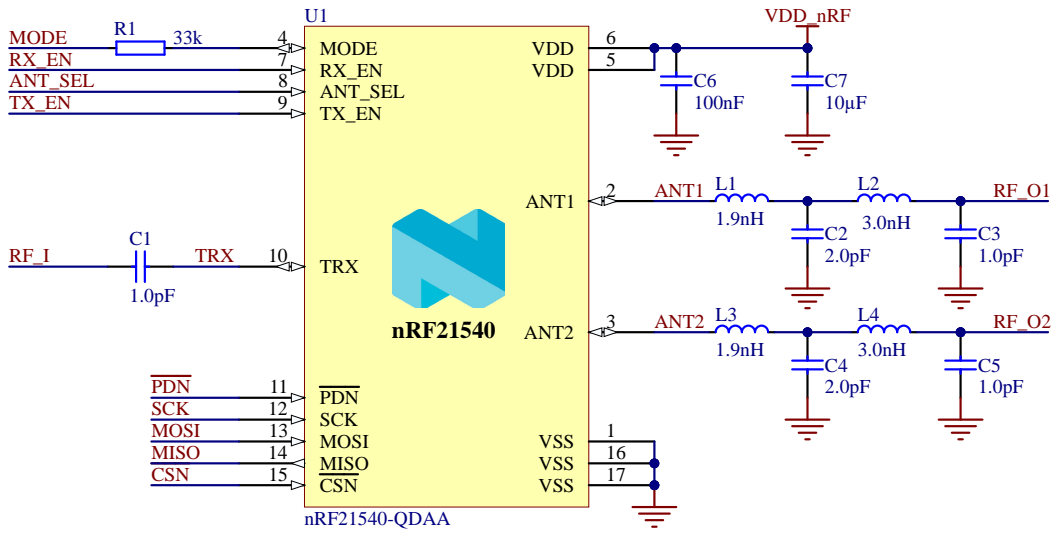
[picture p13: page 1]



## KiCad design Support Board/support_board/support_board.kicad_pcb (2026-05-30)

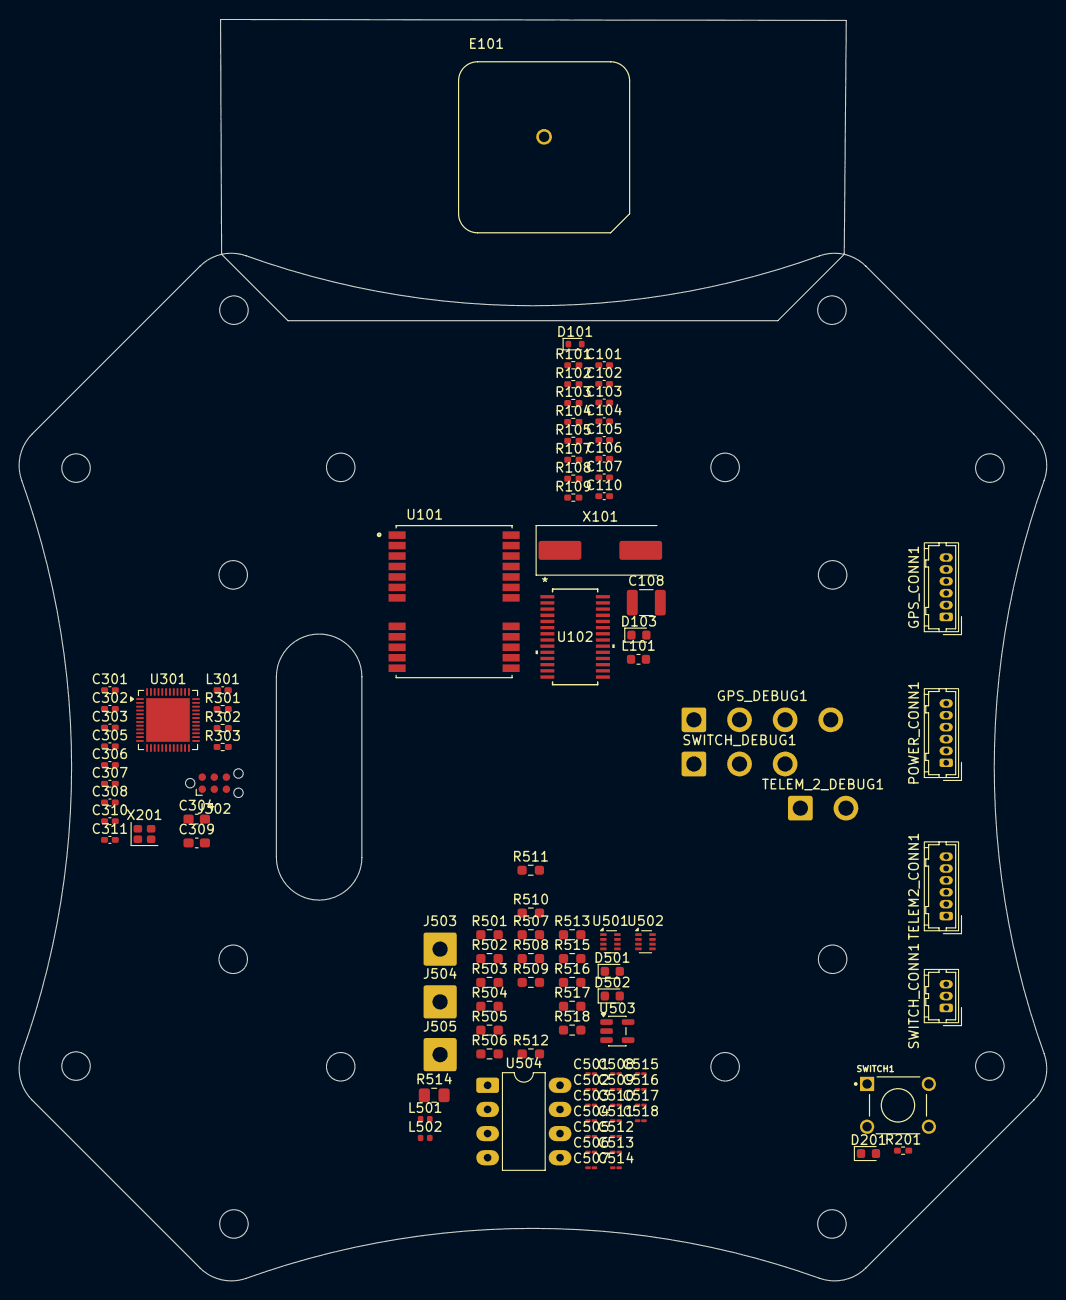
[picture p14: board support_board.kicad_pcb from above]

Board: 4 copper layers, 108.1 x 132.7 mm, 100 parts (1 on the bottom side), 61 nets, no tracks yet.

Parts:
C101: 22pF ±10% 50V; C_0402_1005Metric_Pad0.74x0.62mm_HandSolder
C102: 33pF ±10% 50V; C_0402_1005Metric_Pad0.74x0.62mm_HandSolder
C103: 4.7uF ±10% 10V; C_0402_1005Metric_Pad0.74x0.62mm_HandSolder
C104, C105, C107, C110: 100nF ±10% 50V; C_0402_1005Metric_Pad0.74x0.62mm_HandSolder
C106: 10uF ±10% 10V; C_0402_1005Metric_Pad0.74x0.62mm_HandSolder
C108: XH414HG-IV01E; C_1210_3225Metric
C301, C302: 12pF; C_0402_1005Metric_Pad0.74x0.62mm_HandSolder
C303, C305, C306, C307, C308: 100nF; C_0402_1005Metric_Pad0.74x0.62mm_HandSolder
C304: 22 uF; C_0603_1608Metric_Pad1.08x0.95mm_HandSolder
C309: 0.3pF; C_0603_1608Metric_Pad1.08x0.95mm_HandSolder
C310: 0.5pF; C_0402_1005Metric_Pad0.74x0.62mm_HandSolder
C311: 10nF; C_0402_1005Metric_Pad0.74x0.62mm_HandSolder
C501, C502: 10 u; C_01005_0402Metric_Pad0.57x0.30mm_HandSolder
C503, C510, C516, C517: 100n; C_01005_0402Metric_Pad0.57x0.30mm_HandSolder
C504, C511: 22 n; C_01005_0402Metric_Pad0.57x0.30mm_HandSolder
C505, C512: 100 n; C_01005_0402Metric_Pad0.57x0.30mm_HandSolder
C506, C513: 22u; C_01005_0402Metric_Pad0.57x0.30mm_HandSolder
C507, C514: 22µ; C_01005_0402Metric_Pad0.57x0.30mm_HandSolder
C508: 470p; C_01005_0402Metric_Pad0.57x0.30mm_HandSolder
C509: 22 u; C_01005_0402Metric_Pad0.57x0.30mm_HandSolder
C515: 300p; C_01005_0402Metric_Pad0.57x0.30mm_HandSolder
C518: 1µ; C_01005_0402Metric_Pad0.57x0.30mm_HandSolder
D101: RB520S30T1G; D_SOD-523
D103: GREEN; LED_0603_1608Metric
D201, D501: RED; LED_0603_1608Metric
D502: YELLOW; LED_0603_1608Metric
E101: APAE1575R1820ABDC1-T; XDCR_APAE1575R1820ABDC1-T
GPS_CONN1: Conn_01x06_Socket; Hirose_DF13-06P-1.25DSA_1x06_P1.25mm_Vertical
GPS_DEBUG1: Conn_01x04_Socket; SolderWire-0.75sqmm_1x04_P4.8mm_D1.25mm_OD2.3mm
J301: Conn_Coaxial; U.FL_Hirose_U.FL-R-SMT-1_Vertical
J302: Conn_ARM_SWD_TagConnect_TC2030-NL; Tag-Connect_TC2030-IDC-NL_2x03_P1.27mm_Vertical
J503, J504, J505: Conn_01x01_Socket; SolderWire-0.75sqmm_1x01_D1.25mm_OD3.5mm
L101: 22uH ±10%; L_0603_1608Metric
L301: 2nH; L_0402_1005Metric_Pad0.77x0.64mm_HandSolder
L501, L502: 6.8µH; L_0402_1005Metric
POWER_CONN1: Conn_01x06_Socket; Hirose_DF13-06P-1.25DSA_1x06_P1.25mm_Vertical
R101, R107, R109: 1K ±1%; R_0402_1005Metric_Pad0.72x0.64mm_HandSolder
R102, R103: 10K ±1%; R_0402_1005Metric_Pad0.72x0.64mm_HandSolder
R104, R105: 4.7K ±1%; R_0402_1005Metric_Pad0.72x0.64mm_HandSolder
R108: 22R ±1%; R_0402_1005Metric_Pad0.72x0.64mm_HandSolder
R201: 220; R_0402_1005Metric_Pad0.72x0.64mm_HandSolder
R301: 10k; R_0402_1005Metric_Pad0.72x0.64mm_HandSolder
R302, R303: 100; R_0402_1005Metric_Pad0.72x0.64mm_HandSolder
R501, R507: 191k; R_0603_1608Metric_Pad0.98x0.95mm_HandSolder
R502, R508: 49.9k; R_0603_1608Metric_Pad0.98x0.95mm_HandSolder
R503: 100k; R_0603_1608Metric_Pad0.98x0.95mm_HandSolder
R504, R509, R510, R511, R516: 10k; R_0603_1608Metric_Pad0.98x0.95mm_HandSolder
R505: 9.09k; R_0603_1608Metric_Pad0.98x0.95mm_HandSolder
R506: 51k; R_0603_1608Metric_Pad0.98x0.95mm_HandSolder
R512: 90.9k; R_0603_1608Metric_Pad0.98x0.95mm_HandSolder
R513: 56k; R_0603_1608Metric_Pad0.98x0.95mm_HandSolder
R514: 12k; C_0805_2012Metric_Pad1.18x1.45mm_HandSolder
R515: 4m; R_0603_1608Metric_Pad0.98x0.95mm_HandSolder
R517, R518: 1K ±1%; R_0603_1608Metric_Pad0.98x0.95mm_HandSolder
SWITCH1: 1825910-6; SW_1825910-6-4
SWITCH_CONN1: Conn_01x03_Socket; Hirose_DF13-03P-1.25DSA_1x03_P1.25mm_Vertical
SWITCH_DEBUG1: Conn_01x03_Socket; SolderWire-0.75sqmm_1x03_P4.8mm_D1.25mm_OD2.3mm
TELEM2_CONN1: Conn_01x06_Socket; Hirose_DF13-06P-1.25DSA_1x06_P1.25mm_Vertical
TELEM_2_DEBUG1: Conn_01x02_Socket; SolderWire-0.75sqmm_1x02_P4.8mm_D1.25mm_OD2.3mm
U101: NEO-M8N; NEO-M8N-0
U102: SC16IS752
U301: nRF54L15-QFXX; QFN-48-1EP_6x6mm_P0.4mm_EP4.6x4.6mm
U501, U502: MP2338; SOT-583-8
U503: INA169; SOT-23-5
U504: MCP6002T-E/OT; DIP-8_W7.62mm_LongPads
X101: 3.072MHZ; Crystal_SMD_HC49-SD
X201: Crystal_GND24; Crystal_SMD_2016-4Pin_2.0x1.6mm

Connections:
3V3: C105.2, C106.2, C107.2, C110.2, C303.1, C304.1, C506.1, C507.1, C508.2, C516.1, C517.1, C518.1, J302.1 (VCC), L501.2, R101.2, R102.2, R103.2, R104.2, R105.2, R301.1, R503.2, R506.2, R518.2, U101.7 (VDD_USB), U101.23 (VCC), U102.8 (VDD), U301.10 (VDD), U301.22 (VDD), U301.36 (VDD), U301.47 (VDD), U301.48 (VDD), U503.5 (V+), U504.8 (V+)
5V: C513.1, C514.1, C515.2, L502.2, R509.2, R512.2, R517.2
/GPS/IRQ: R101.1, U102.15 (~IRQ)
/GPS/RESET: R103.1, U102.5 (~RESET)
/GPS/RXD_GPS: U101.21 (RXD), U102.3 (TXA)
/GPS/TXD_GPS: U101.20 (TXD), U102.4 (RXA)
/connectors/5V: POWER_CONN1.1, POWER_CONN1.2
/connectors/GND: GPS_CONN1.5, POWER_CONN1.5, POWER_CONN1.6, TELEM2_CONN1.6
/connectors/RXD_GPS: GPS_CONN1.3, GPS_DEBUG1.3
/connectors/RXD_TELEM2: TELEM2_CONN1.3, TELEM_2_DEBUG1.2
/connectors/SWITCH_LED: SWITCH_CONN1.2, SWITCH_DEBUG1.3
/connectors/SWITCH_OUT: SWITCH_CONN1.3, SWITCH_DEBUG1.2
/connectors/SWITCH_VCC: SWITCH_CONN1.1, SWITCH_DEBUG1.1
/connectors/TXD_GPS: GPS_CONN1.4, GPS_DEBUG1.4
/connectors/TXD_TELEM2: TELEM2_CONN1.2, TELEM_2_DEBUG1.1
/power/CURRENT_SENSE: J504.1, U504.6 (-), U504.7
/power/VOLTAGE_SENSE: J503.1, U504.1, U504.2 (-)
/power/V_bat: C501.1, C502.1, C503.1, C509.1, C510.1, R501.1, R507.1, R515.2, U501.2 (VIN), U502.2 (VIN), U503.4 (-)
/power/V_bat_in: R513.1, R515.1, U503.3 (+)
GND: C101.1, C102.1, C103.1, C104.1, C105.1, C106.1, C107.1, C110.1, C301.2, C302.1, C303.2, C304.2, C305.2, C306.2, C307.2, C308.2, C309.2, C310.2, C311.1, C501.2, C502.2, C503.2, C504.2, C506.2, C507.2, C509.2, C510.2, C511.2, C513.2, C514.2, C516.2, C517.2, C518.2, J301.2 (Ext), J302.5 (GND), J505.1, R502.2, R505.1, R508.2, R511.1, R514.2, R516.2, U101.10 (GND@1), U101.12 (GND@2), U101.13 (GND@3), U101.24 (GND@4), U102.10 (A0), U102.11 (A1), U102.22 (VSS), U301.32 (VSS_PA), U301.44 (VSS), U301.49 (VSS), U501.4 (GND), U502.4 (GND), U503.2 (GND), U504.4 (V-), X201.2 (G), X201.4 (G)
unnamed: C508.1, R504.2, R505.2, R506.1
unnamed: C515.1, R510.2, R511.2, R512.1
unnamed: D201.1 (K), R201.1
unnamed: C309.1, C310.1, J301.1 (In), L301.2
unnamed: J302.4 (SWCLK), R302.2
unnamed: J302.2 (SWDIO), R303.2
unnamed: C311.2, J302.3 (~RESET), R301.2, U301.30 (~RESET)
unnamed: L101.1, R108.2
unnamed: R108.1, U101.8 (REST_N), U101.9 (VCC_RF)
unnamed: E101.1, L101.2, U101.11 (RF_IN)
unnamed: R107.2, U101.3 (TIMEPULSE)
unnamed: C103.2, C104.2, R109.2, U101.22 (V_BCKP)
unnamed: R102.1, U102.9 (I2C)
unnamed: C101.2, U102.6 (XTAL1), X101.2
unnamed: C102.2, U102.7 (XTAL2), X101.1
unnamed: L301.1, U301.31 (ANT)
unnamed: C308.1, U301.46 (DCC)
unnamed: C305.1, U301.43 (DECA)
unnamed: C307.1, U301.45 (DECD)
unnamed: C306.1, U301.33 (DECRF)
unnamed: R302.1, U301.26 (SWDCLK)
unnamed: R303.1, U301.25 (SWDIO)
unnamed: C302.2, U301.34 (XC1), X201.1
unnamed: C301.1, U301.35 (XC2), X201.3
unnamed: C505.1, U501.5 (BST)
unnamed: R501.2, R502.1, U501.6 (EN)
unnamed: R504.1, U501.8 (FB)
unnamed: R503.1, U501.1 (PG)
unnamed: C504.1, U501.7 (SS)
unnamed: C505.2, L501.1, U501.3 (SW)
unnamed: C512.1, U502.5 (BST)
unnamed: R507.2, R508.1, U502.6 (EN)
unnamed: R510.1, U502.8 (FB)
unnamed: R509.1, U502.1 (PG)
unnamed: C511.1, U502.7 (SS)
unnamed: C512.2, L502.1, U502.3 (SW)
unnamed: R513.2, R514.1, U504.3 (+)
unnamed: R516.1, U503.1, U504.5 (+)
SCL: GPS_CONN1.1, GPS_DEBUG1.1, R104.1, U102.13 (SCL)
SDA: GPS_CONN1.2, GPS_DEBUG1.2, R105.1, U102.14 (SDA)
SWITCH_VCC: D201.2 (A), SWITCH1.1

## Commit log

2026-05-01 FIrst Commit: PM Test Board
    [power_management_test.kicad_pcb, power_management_test.kicad_sch]
2026-05-01 Added BOM
    [BOM_PM_Test.csv]
2026-05-04 Updated BOM and fixed minor mismatches
    [BOM_PM_Test.csv, power_management_test.kicad_pcb]
2026-05-07 Final Check
    [BOM Support Board - PM_Test.csv, BOM_power_management.csv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]
2026-05-30 Added Current Support
    Added nRF ICs.
    [connectors.kicad_sch, gps.kicad_sch, importer.kicad_pcb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]
2026-06-02 Updated PM files and Schematics in the Support Board
    [400708.DRL, 400708.GBL, 400708.GBO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]
2026-06-05 Add layout notes for support board design
